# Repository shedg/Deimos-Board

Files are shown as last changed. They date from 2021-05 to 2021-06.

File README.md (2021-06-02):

# Deimos-Board
A small and easy to use PID heater 

## OVERVIEW
The mod itself consist of a small circuit board with just a couple of components that is designed to accept an arduino nano board to control a powerfull mosfet, the arduino itself works as a PID controller and can be easily configured to use any passive thermistor (usually a glass bead PTC resistor used in FDM printers) and heater up to 150W, an LCD is used for a simple GUI and three push buttons are used to set the desired temperature.

### I/Os

-Input voltage is 12V typical, but can work at 24V (might need a little heatsink on one of the components).

-Output is a PWM signal with the value of the Input voltage, the board itself should be able to pilot loads up to 150W DC and still have some safety margin, typical value is 100W and that is plenty to heat the enclosure of the printer even 15 °C above ambient temperature with no problems.

-Optional always on terminal is straight up connected to the input voltage, ideally it's to use with a small fan to circulate the hot air in the enclosure.

-The thermistor Terminal is coupled with a resistor to ensure correct reading of the temperature, you can use any passive thermistor as long as you couple it with the correct value resistor, typically used is a PTC 100k glass bead thermistor coupled with a 100k ohm resistor, cheaply available as it's the standard FDM thermistor.

### Display

On the board these is a predisposition for standard character LCD, the firmware itself is prepared to use a 1602 LCD to write the temperature data, to use a backlit display you just need to connect the two terminals to the optional header in the back or for a cleaner solution to jump the on-board resistor and tap into the 5V display wire directly when making the display cable.

### User input and temperature set

The interface is simple: current temperature on the left and set temperature on the right of the display, pressing SET button will enter set-mode (a small arrow will flash near the set temperature) and you can use the UP and DOWN buttons to set the desired temperature in the enclosure, pressing SET again will exit set mode.
When booting up the set temperature is at a safe low value to ensure the heater won't be immediately turned on, that value can be set in the firmware to a different value if you wish to just turn the entire board on and off when needed with always the same setpoint.

### 3D printed parts

A small enclosure for the board and the interfacing components need to be printed or made in some way to ensure the board itself is not exposed and to protect from unwanted shorts or damage, the small footprint of the board itself should make it an easy print job for any FDM printer or even slightly bigger resin printers and shouldn't take much space near the resin printer that you want to add this upgrade to. Additional prints or modification are required to securely hold the chosen heater inside the printer itself.

### Customization

The board itself is very modular, you can use a lot of different options for heaters, thermistors,buttons and display with some minor limitation aspect you have to consider for it to work. The core structure of the firmware makes it easy to change key parameters such as the thermistor values and you have the option of power-limiting the heater to a certain percentage or change the PID parameters for a slower or quicker response (only suggest that if you are sure of what you are doing).

### The kit itself

The board is populated by just a bunch of throughhole components, some screw terminals and for the display and arduino it actually uses pin-headers so nothing too difficult to manually solder and i’ll make a nice little schematic to ensure anyone can assemble one correctly. i can also prepare populated boards ready to go for a little extra or you can buy the PCB only and just get your components locally while checking the component list. For the heater and PSU you’ll have to find one yourself but they are easily available on amazon so it’s not a problem.

	Useful links
  [The component checklist](https://docs.google.com/spreadsheets/d/1y2S4blwJZZ-803kOBqK99VzKAkgP2FpXWgCPjR_RUzY/edit#gid=1386834576) 

  [Heater mount i use](https://www.thingiverse.com/thing:4305321)
	
	Libraries used:	
[Ace button 1.8.0](https://github.com/bxparks/AceButton)

[AutoPID 1.0.3](https://r-downing.github.io/AutoPID/)

[NTC Thermistor 2.0.3](https://github.com/YuriiSalimov/NTC_Thermistor)

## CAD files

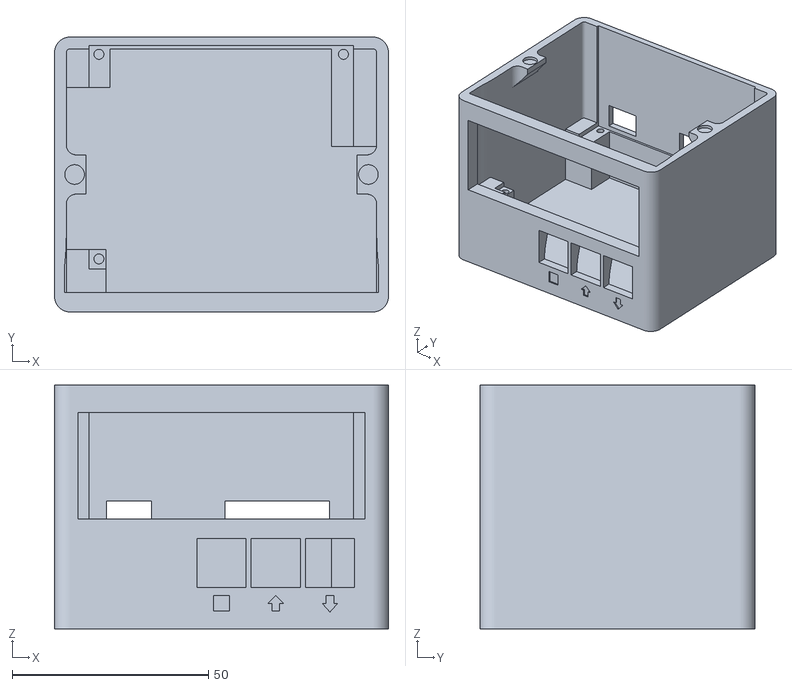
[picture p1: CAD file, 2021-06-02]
DEIMOS Chassis example/Main body.stl
85.0 x 70.0 x 62.0

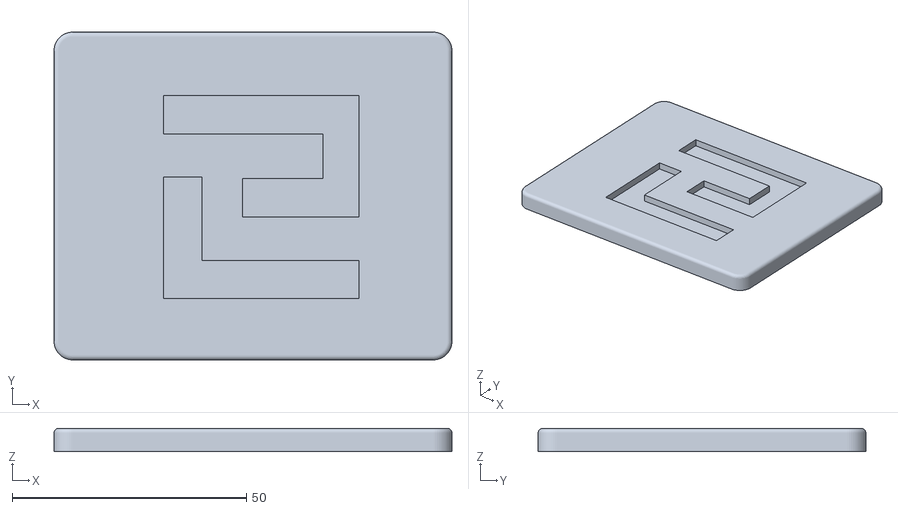
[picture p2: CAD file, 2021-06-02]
DEIMOS Chassis example/TOP.stl
85.0 x 70.0 x 5.00

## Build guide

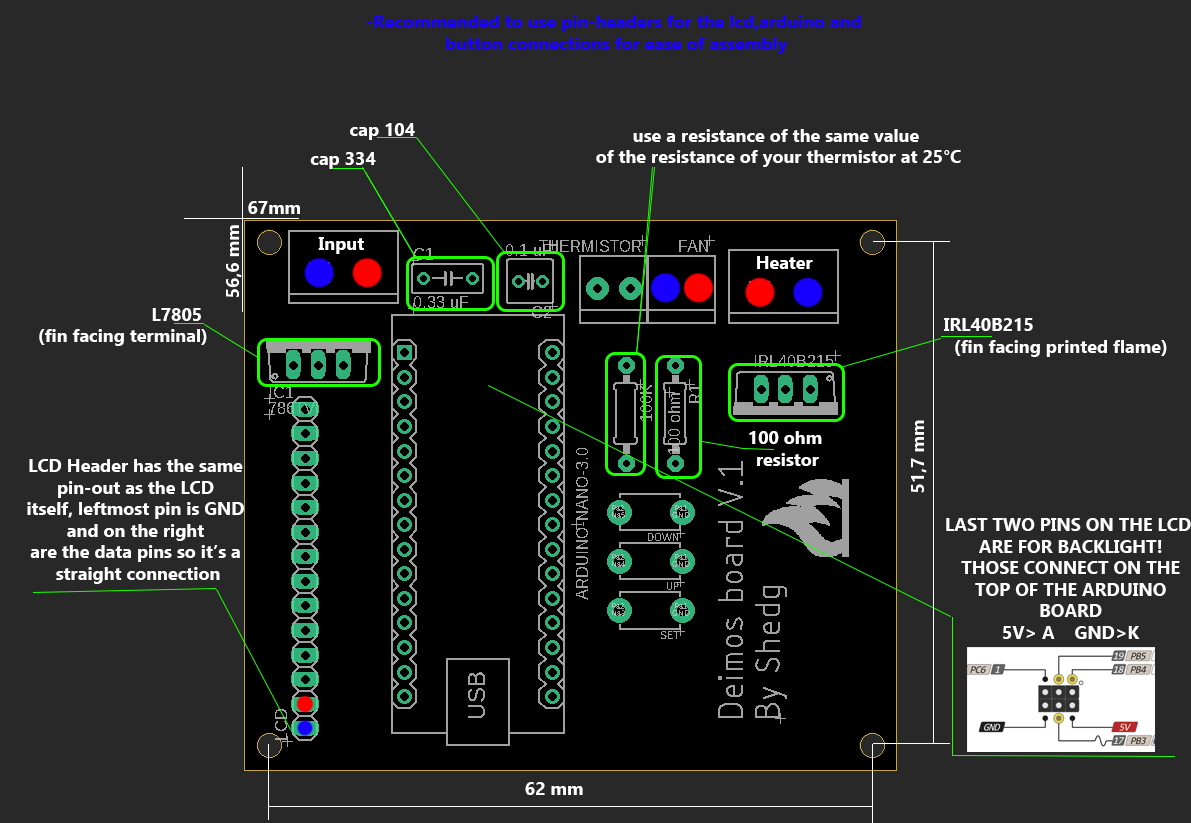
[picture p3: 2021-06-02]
Assembly-guide.jpg

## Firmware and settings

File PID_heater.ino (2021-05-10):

#include <AutoPID.h>             //nice quick PID with variable parameters, has an aggressive curve when far away and then tries to smooth to a nice lower value to prevent overshoot
#include <Thermistor.h>         //these 3 are all for making a simple and quick thermistor reading
#include <NTC_Thermistor.h>
#include <AverageThermistor.h>
#include <LiquidCrystal.h>      //just to use a simple LCD screen to display temperatures
#include <AceButton.h>
using namespace ace_button;
//------------------------------------------------------------------------------------------
//------------------------------------------------------------------------------------------
//------------------------------------------------------------------------------------------
/*LCD SETUP----------------------------------------------------------------------------------------
initialize the library by associating any needed LCD interface pin
 with the arduino pin number it is connected to*/
 
const int rs = 12, en = 11, d4 = 10, d5 = 9, d6 = 8, d7 = 7;
LiquidCrystal lcd(rs, en, d4, d5, d6, d7);

const int Contrast_Pin = A4;

//this one is to print a custom arrow on the LCD
byte customChar[] = {
  B00100,
  B00110,
  B00011,
  B11111,
  B11111,
  B00011,
  B00110,
  B00100
};

//BUTTONS SETUP--------------------------------------------------------------------------------------

//3 buttons, SET,UP and DOWN to manage the setpoint
const int  SETPin = A1;
const int  UPPin = A2;
const int  DOWNPin = A3;

AceButton SET(SETPin);
AceButton UP(UPPin);
AceButton DOWN(DOWNPin);

//even handler for the buttons
void handleEvent(AceButton*, uint8_t, uint8_t);

//index for the setting mode
bool setting =0;

//THERMISTOR SETUP-------------------------------------------------------------------------------------

//Values for the thermistor, it's set to an average glass bead thermistor for 3D printers
#define SENSOR_PIN             A0 //A0
#define REFERENCE_RESISTANCE   100000
#define NOMINAL_RESISTANCE     100000
#define NOMINAL_TEMPERATURE    25
#define B_VALUE                3950

/**
  How many readings are taken to determine a mean temperature.
  The more values, the longer a calibration is performed,
  but the readings will be more accurate.
*/
#define READINGS_NUMBER 10

/**
  Delay time between a temperature readings
  from the temperature sensor (ms).
*/
#define DELAY_TIME 10

//creating the thermistor
Thermistor* thermistor = NULL;

//PID SETUP---------------------------------------------------------------------------------

//pid settings and gains
#define OUTPUT_MIN 0
#define OUTPUT_MAX 255
#define KP 2 //.12
#define KI 5 //.0003
#define KD 1 //0
#define OUTPUT_PIN 5 //D5 this is the pin that drives the mosfet for the heater

//Define Variables for the PID we'll be connecting to
double Setpoint, Input, Output;

//input/output variables passed by reference, so they are updated automatically
AutoPID myPID(&Input, &Setpoint, &Output, OUTPUT_MIN, OUTPUT_MAX, KP, KI, KD);

//------------------------------------------------------------------------------------------
//------------------------------------------------------------------------------------------
//------------------------------------------------------------------------------------------

void setup() {
  
  //setting up the button's pins and index number
  // Button uses the built-in pull up register.
  pinMode(SETPin, INPUT_PULLUP);
  pinMode(UPPin, INPUT_PULLUP);
  pinMode(DOWNPin, INPUT_PULLUP);

  SET.init(SETPin);
  UP.init(UPPin);
  DOWN.init(DOWNPin);

  ButtonConfig* buttonConfig = ButtonConfig::getSystemButtonConfig();
  buttonConfig->setEventHandler(handleEvent);
  buttonConfig->setFeature(ButtonConfig::kFeatureClick);
  int clickDelay=100;
  void setClickDelay(uint16_t clickDelay);
  
  
  //set the contrast pin on the display 
  pinMode(Contrast_Pin, OUTPUT);
  analogWrite(Contrast_Pin, 5);
  
  // set up the LCD's number of columns and rows and prepares the display so that it only has to update the numbers
  lcd.clear();
  lcd.begin(16, 2);
  lcd.print("Current:   Set:");
  lcd.createChar(0, customChar);
  
  //THERMISTOR SETUP
  Serial.begin(115200);

  Thermistor* originThermistor = new NTC_Thermistor(
    SENSOR_PIN,
    REFERENCE_RESISTANCE,
    NOMINAL_RESISTANCE,
    NOMINAL_TEMPERATURE,
    B_VALUE
  );
  thermistor = new AverageThermistor(
    originThermistor,
    READINGS_NUMBER,
    DELAY_TIME
  );

  //PID SETUP
  
  //initialize the variables we're linked to
  Input = thermistor->readCelsius(); //uses the thermistor library to read the temperature in °C
  
  Setpoint = 15; //so that when turning it on it will always be a safe value and won't turn on the heater unless we set a temperature

  pinMode(OUTPUT_PIN, OUTPUT);
  //if temperature is more than 4 degrees below or above setpoint, OUTPUT will be set to min or max respectively
  
  //set PID update interval (ms)
  myPID.setTimeStep(40);
}


void loop() {
  
  
  //writes on the display the current temperatures 
  lcd.setCursor(0, 1);
  lcd.print(Input, 1);
  lcd.write(B11011111);
  lcd.print("C");
  lcd.setCursor(11, 1);
  lcd.print(Setpoint);
    
  //check buttons status
   SET.check();
   
  if(setting==1)
  {
    lcd.setCursor(10, 1);
    lcd.write(byte(0)); 
    UP.check();
    DOWN.check();
  }
  else
  {
    lcd.setCursor(10, 1);
    lcd.print(" ");
  }
  
  
  Input = thermistor->readCelsius();
  Serial.print("Input: ");
  Serial.println(Input);
  myPID.run();
  Serial.print("Output: ");
  Serial.println(Output);
  analogWrite(OUTPUT_PIN, Output);

  
}

//handler for the buttons to check input
void handleEvent(AceButton* button, uint8_t eventType, uint8_t buttonState) {
  
   switch (eventType){
    case AceButton::kEventPressed:{
      switch (button->getPin()){
        case SETPin :         
          setting=!setting;
          break;
        case UPPin :
          Setpoint++;
          break;
        case DOWNPin :
          Setpoint--;
          break;
        }
    }
 }
}

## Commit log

2021-05-10 Add files via upload
    The main Code for the arduino board, it should be easily adjustable for your needs
2021-06-02 Add files via upload
    A basic chassis for the board, and the fusion file if you need to slightly edit it (watch out, i'm a messy guy when using fusion so lots of garbage sketches and stuff in the model itself)
    [Main body.stl, TOP.stl]
